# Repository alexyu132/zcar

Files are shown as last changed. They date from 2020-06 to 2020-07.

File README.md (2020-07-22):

This is a 1/28 scale RC chassis designed to be compatible with Kyosho MINI-Z body shells. Current version fits 90mm (M) wheelbase shells.

Video: https://www.youtube.com/watch?v=_t0HLC2bZMU

zcar image

## Features: 
- Independent front suspension and hinged rear suspension
- Ackermann steering geometry with 45 degree max steering angle
- Uses common and cheap parts (625 bearings, M3 hardware)
- Low part count and variety - only 3 different screw lengths needed; locknuts everywhere

## New in 1.1:
- More robust rear bearing assembly
- Front suspension travel reduced to prevent scraping
- Redesigned front body mount for increased ground clearance
- Reduced height of motor mount and rear suspension frame to fit lower profile shells

## Non-printed Parts List

|  Part | Quantity | Notes  |
|---|---|---|
|  M3x20mm button head screw | 7  | |
|  M3x14mm button head screw | 2 | |
|  M3x10mm button head screw | 8  | |
|  M3 lock nut | 17 | |
| 625 bearing | 4 | |
| 130 size brushed motor, 2s compatible | 1 | |
| SG90 micro servo | 1 | |
| Compression spring, ~4mm OD, ~5mm length | 2 | For front suspension. Softer springs are better.  Springs from multicolor retractable pens work well here when cut to length. Ordinary pen springs are too stiff. |
| Compression spring, ~4mm OD, ~22mm length | 2 | For rear suspension. Springs from multicolor retractable pens work well here. Can cut to length or leave uncut for different suspension stiffnesses.|
| Venom Fly 300mah 2S battery or RDQ Series 2S 350mAh LiHV battery | 1 | Batteries up to approx. 45x23x16mm should fit |
| Small brushed ESC, 2S compatible | 1 |
| Small radio receiver | 1 | 2 channels or more, smaller than approx 34x22x13mm. Flysky GR3E works if decased. |
| MINI-Z shell | 1 | Tested with Kyosho MZQ101 AE86 shell |
| MINI-Z tires | 4 | 8.5mm width, 25mm OD, 20mm ID. The tires that come with MINI-Z shells work fine. |

## Printing Notes:
###  Settings
#### Resolution: 0.1-0.15mm

#### Infill: 25% or higher

#### Vertical perimeters: 3 or more

#### Horizontal perimeters: 4 or more

#### Supports: Off
Most of the printed parts are split into 2 prearranged trays. **Print tray1.stl at 0.15mm layer height and tray2.stl at 0.1mm layer height**. Make sure your printer has good layer adhesion, as some parts have a small bed contact area and can warp or detach easily.

The front wheels have a cylindrical piece of built-in support on the inside of the wheel. To remove, use pliers to grip the support and pull straight out without twisting.

The motor mount and gears are located in the geartrains subfolder in the STL folder. **There are currently 4 gear ratios available: 13T:42T, 11T:43T, 10T:43T, and 9T:43T**. Generally a lower gear ratio (fewer teeth on motor pinion) is preferred unless your motor is designed for low speed/high torque.

For each gearing option, there are loose and tight motor mounts available due to 130 motors varying slightly in size. The loose mount fits motors that are 15.4mm wide across the flats, while the tight mount fits 15mm wide motors. If you decide to change the gearing, make sure to also print a matching motor mount, as motor mounts are not interchangeable among different geartrains. For more powerful motors, you may need to print the pinion and motor mount in ABS or PETG to prevent heat-induced softening.

## Assembly
Coming soon

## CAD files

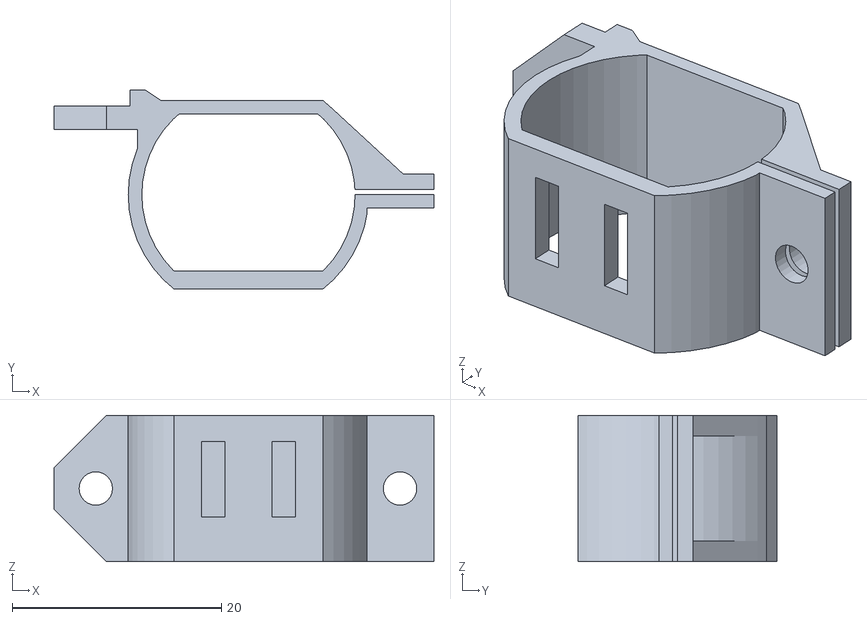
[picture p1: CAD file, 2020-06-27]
stl/geartrains/10T-43T/motor_mount_10_43_tight.stl
36.4 x 19.0 x 14.0

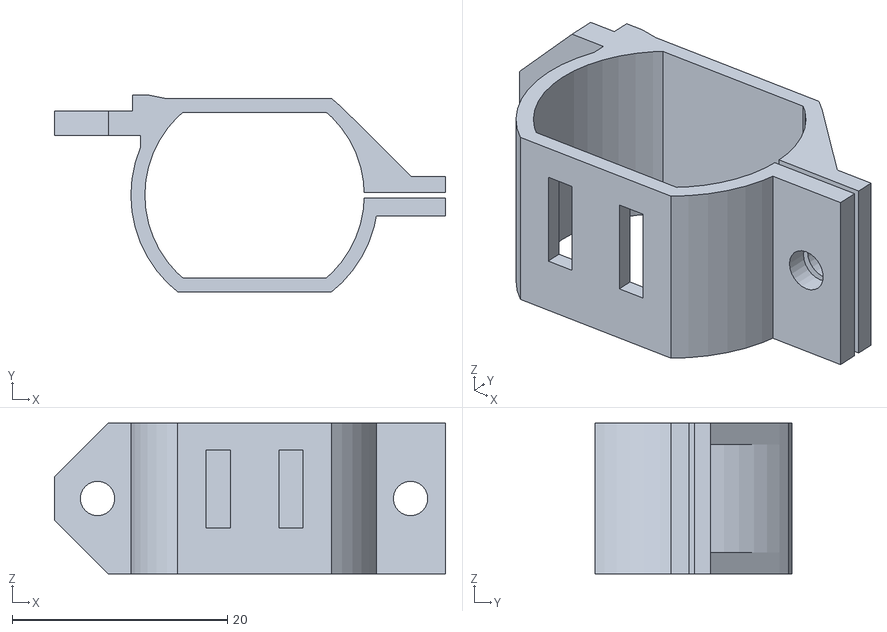
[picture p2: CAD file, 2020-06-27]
stl/geartrains/13T-42T/motor_mount_13_42_loose.stl
36.4 x 18.3 x 14.0

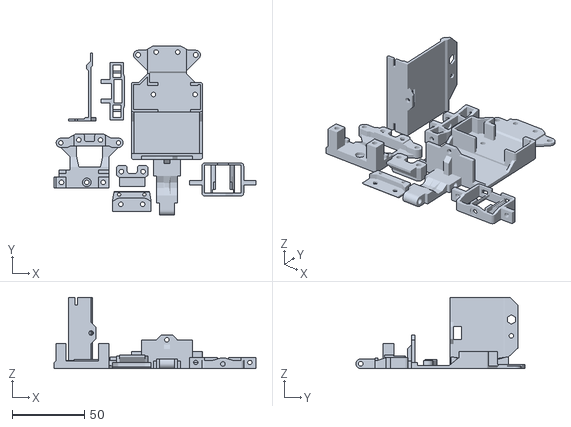
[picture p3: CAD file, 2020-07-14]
stl/tray1.stl
140.2 x 117.4 x 49.5

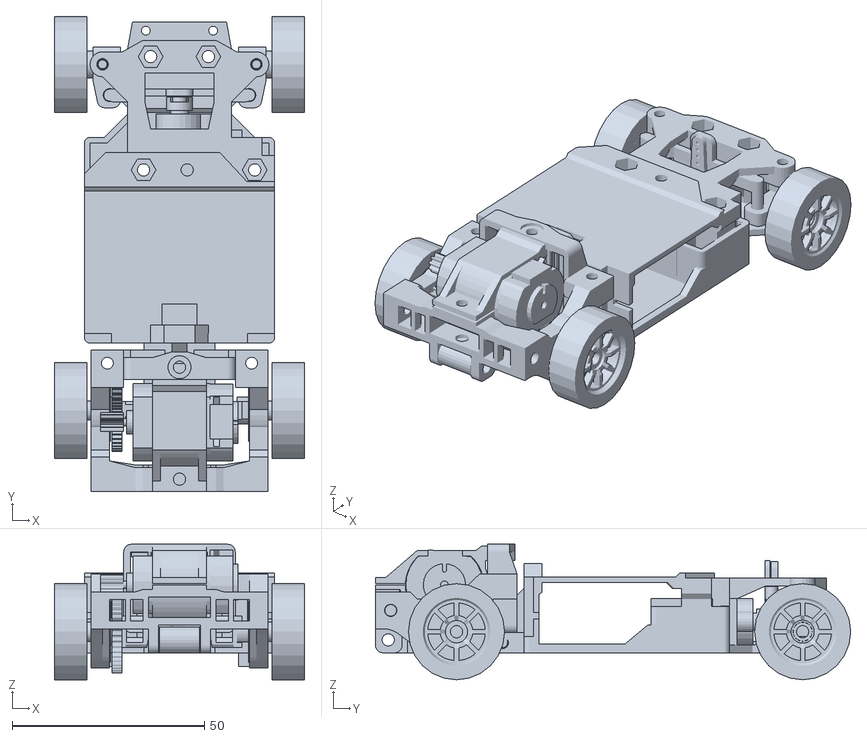
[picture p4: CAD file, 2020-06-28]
stl/zcar.stl
65.0 x 123.6 x 35.2

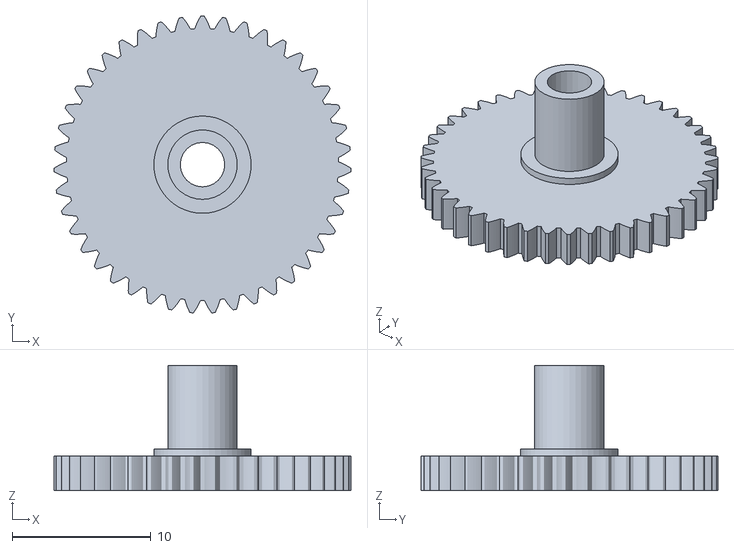
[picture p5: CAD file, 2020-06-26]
stl/geartrains/10T-43T/43T_gear.stl
21.4 x 21.4 x 9.00

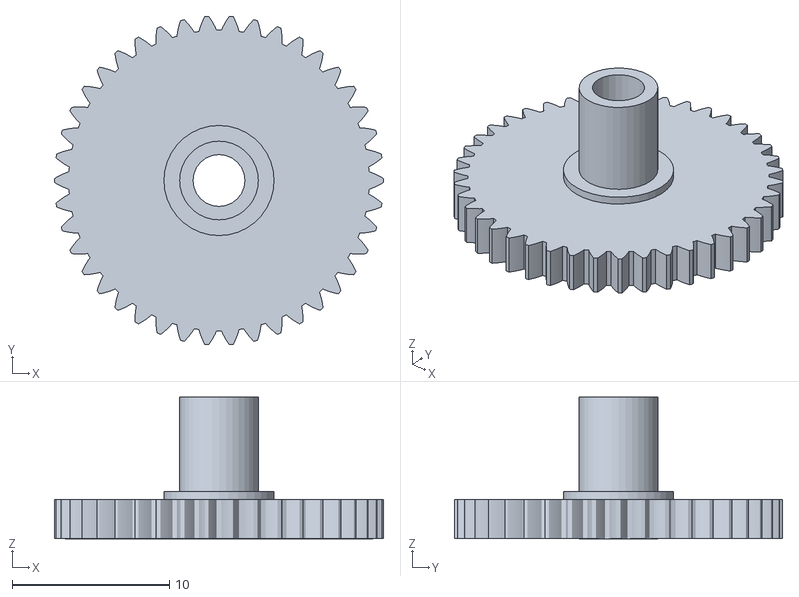
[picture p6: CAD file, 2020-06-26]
stl/geartrains/13T-42T/42T_gear.stl
20.9 x 20.9 x 9.01

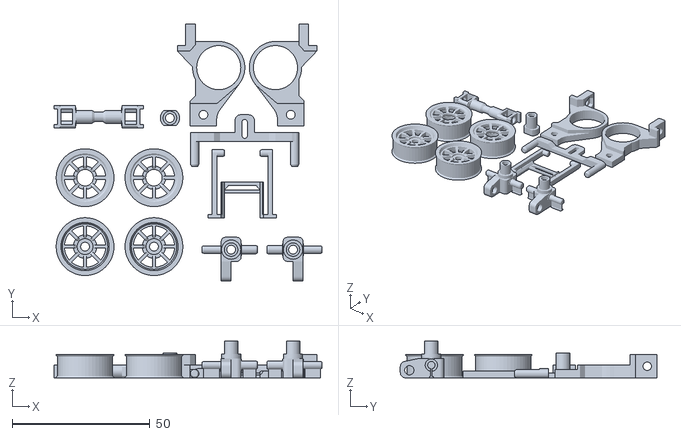
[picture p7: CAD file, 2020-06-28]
stl/tray2.stl
97.2 x 93.1 x 13.4

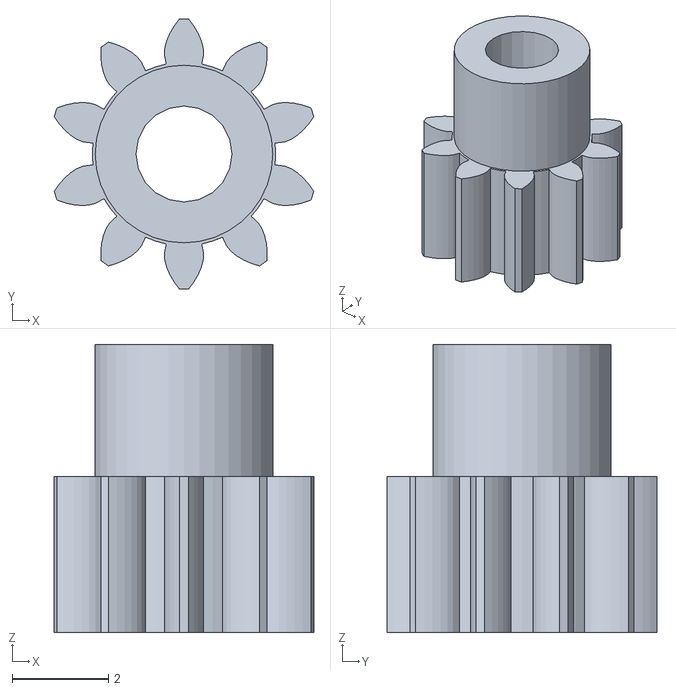
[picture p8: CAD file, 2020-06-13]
stl/geartrains/10T-43T/10T_pinion.stl
5.41 x 5.63 x 6.00

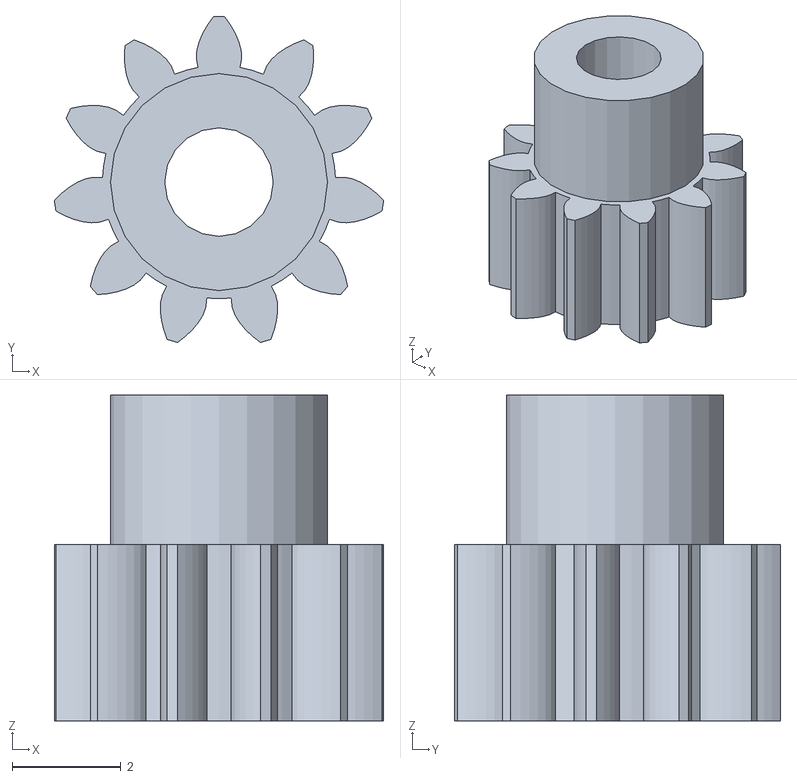
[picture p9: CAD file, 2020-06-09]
stl/geartrains/11T-43T/11T_pinion.stl
6.07 x 6.01 x 6.00

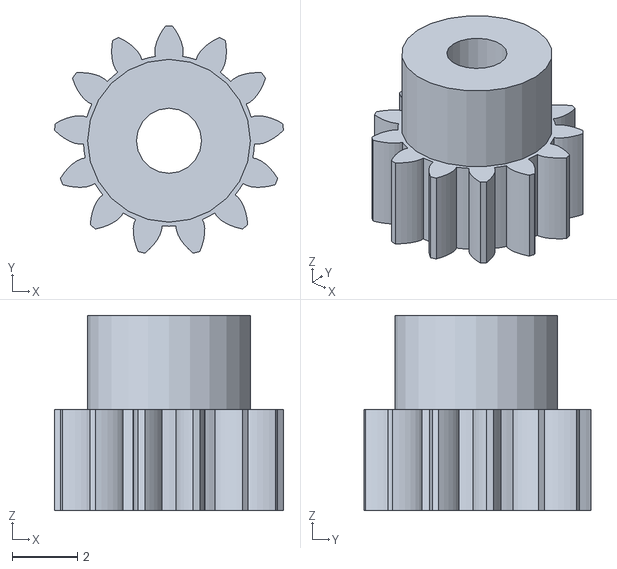
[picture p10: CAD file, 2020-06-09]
stl/geartrains/13T-42T/13T_pinion.stl
7.03 x 6.98 x 6.00

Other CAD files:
stl/geartrains/11T-43T/motor_mount_11_43_tight.stl
stl/geartrains/9T-43T/motor_mount_9_43_loose.stl
stl/geartrains/10T-43T/motor_mount_10_43_loose.stl
stl/geartrains/11T-43T/motor_mount_11_43_loose.stl
stl/geartrains/13T-42T/motor_mount_13_42_tight.stl
stl/geartrains/9T-43T/motor_mount_9_43_tight.stl
stl/geartrains/11T-43T/43T_gear.stl
stl/geartrains/9T-43T/9T_pinion.stl
stl/tpu_tire.stl
zcar.skp

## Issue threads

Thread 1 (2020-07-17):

Rear Bearing Hubs

bryanmonahan, 2020-07-17:
hey Alex,  this is an amazing design.  My friend and I have printed a few and are messing around with them

1. found that the rear bearing holders do not maintain hold on the bearings when heated.   am looking at possibly adding a lip around them to maintain control of the bearing, but then must add a washer on the inside to space out the gear from hitting it.

unknown yet.

alexyu132, 2020-07-17:
What's causing the rear bearings to heat up?

If you switch to the 1.1 branch, I've redesigned the rear bearings to be press fit, which should be less flimsy than the previous design (no lip, but I can add one if there are still loosening issues). You could try switching to that, or look into using a higher temp material like PETG or ABS.

bryanmonahan, 2020-07-17:
I am using a complete petg build at the moment...

I have no idea whats happening, but myself and another beta tester are having the same issues on two different builds.

1.1 branch...?  sorry, github is new language for me.  ill go dig around.

alexyu132, 2020-07-17:
If you go to the main page there should be a small dropdown menu on the left that says 'master'. Click that and you can switch to the 1.1 branch.

bryanmonahan, 2020-07-17:
OK, found.

unknown if this will help.

What is happening, during racing when cornering, the bearings are slipping out under full speed.  the car then exits the turn and alignment is off.   Ive taken to epoxy to keep them in place.

Ive slammed a small ridge on the inside to help keep the bearing from shifting, and was about to print it till you told me about v1.1

I think your new design may eliminate it, but unknown what exactly is causing the issue.   Ill print the new version and the rear assembly block it appears to connect to instead of the old method and give that a try.

Thanks for your work with this.

We have also modified the wheels to a simpler design (no spokes) and extended the rear to 11mm.

Looking at modifying the battery cover to create a lower mounting point for the receiver and ESC to lower center of gravity.

This is by far, the simplest and most effective 3d print 1/28th scale car ive found and printed in about 2 years of doing so.   great work.

alexyu132, 2020-07-17:
Thanks!

Which battery are you using? The one I have pretty much fills the entire battery area so lowering the CG would be difficult without dropping the overall ride height.

bryanmonahan, 2020-07-17:
a 3.7... but my theory is if i flip it on its side, i can cram the battery esc and rx into the same space,   but thats later.

I am reprinting parts in taulman tech-g now, i like the new rear end idea from 1.1, i think the that connecting the rear hubs to two different axis will result in a lot more stability.

if you would like to talk, im on discord - scapegoatRB#8166, my friend and I would be happy to help you at least destroy parts to see if they work.

alexyu132, 2020-07-17:
I'd prefer communicating via GitHub issues since it'll make it easier to track problems and suggested improvements. If the new press-fit design fixes the problem, we can close out this issue, but otherwise I can look into adding a lip to the bearing block.

Closed 2020-07-23.

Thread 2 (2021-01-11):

CAD file and assembly instructions

unauwen, 2021-01-11:
Hey, I really like this project and already started printing the components. But I dont know exactly how to assemble the car. Could you add a few pictures of every side? I would like to cusomize it, would it be possible to get the CAD files?
With kind regards
Unauwen

alexyu132, 2021-01-13:
There are some pictures on the Thingiverse page, as well as an STL of the complete assembly. I designed this in SketchUp, so the CAD file is the SKP file in this repo.

unauwen, 2021-01-13:
Thanks for your reply, maybe some photos of the back Suspension and/or the front steering would be helpfull for other makers, but I figured it out with trial and error. Thanks for the design

Closed 2021-01-13.

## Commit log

2020-05-23 initial work
    [zcar.skp]
2020-05-25 rear axle work
    [zcar.skp]
2020-05-25 suspension adjustments, rear axle work
    [zcar.skp]
2020-05-25 rear suspension work
    [zcar.skp]
2020-05-25 rear suspension
    [zcar.skp]
2020-05-25 fix gear clearance
    [zcar.skp]
2020-05-25 top plate
    [zcar.skp]
2020-05-25 tweak bottom plate
    [zcar.skp]
2020-05-25 reduce material usage
    [zcar.skp]
2020-05-25 small tweaks
    [zcar.skp]
2020-05-25 add supports to steering knuckles
    [zcar.skp]
2020-05-25 rear body tweaks
    [zcar.skp]
2020-05-25 tweak rear
    [zcar.skp]
2020-05-26 Add tire retaining ring on wheels
    [zcar.skp]
2020-05-26 Modify wheel retaining ring, minor body tweak
    [zcar.skp]
2020-05-26 Add readme, minor body tweaks
    [zcar.skp]
2020-05-27 make chassis more compact, fix motor mounting position
    [zcar.skp]
2020-05-27 reduce frame width
    [zcar.skp]
2020-05-27 switch to smaller battery to save space
    [zcar.skp]
2020-05-27 add tire
    [zcar.skp]
2020-05-28 increase track width by 1mm
    [zcar.skp]
2020-05-28 lower gear ratio to 13T/42T
    [zcar.skp]
2020-05-29 minor lower frame tweak
    [zcar.skp]
2020-05-29 Improve wheel support layer adhesion, fix rear wheel shaft interface
    [zcar.skp]
2020-05-29 increase sill height
    [zcar.skp]
2020-05-31 lengthen steering rack pins
    [zcar.skp]
2020-05-31 test better wheel supports
    [zcar.skp]
2020-06-01 small printability and clearance adjustments
    [zcar.skp]
2020-06-01 fix dimension errors, improve supports
    [zcar.skp]
2020-06-01 adjust steering rack tolerance
    [zcar.skp]
2020-06-01 lengthen rear suspension slider
    [zcar.skp]
2020-06-01 additional rear spring length
    [zcar.skp]
2020-06-01 shell mounts
    [zcar.skp]
2020-06-02 fix servo mount
    [zcar.skp]
2020-06-02 reduce rear suspension travel
    [zcar.skp]
2020-06-02 add rear suspension alignment tabs
    [zcar.skp]
2020-06-02 fix battery dimensions
    [zcar.skp]
2020-06-02 improve shell fit
    [zcar.skp]
2020-06-03 wheel option for non printed tires
    [zcar.skp]
2020-06-03 reduce track width by 2mm
    [zcar.skp]
2020-06-03 reduce rear suspension spring length, lower top plate
    [zcar.skp]
2020-06-03 0.5mm more front suspension travel
    [zcar.skp]
2020-06-03 slightly thicken sills
    [zcar.skp]
2020-06-04 fix gear clearance error
    [zcar.skp]
2020-06-04 rear assembly improvements
    [zcar.skp]
2020-06-04 tweak steering rack clearances
    [zcar.skp]
2020-06-05 slightly recess rear wheel bolt
    [zcar.skp]
2020-06-06 Add stls, update readme
    [tray1.stl, tray2.stl, zcar.stl]
2020-06-07 slightly extend rear suspension slider
    [tray1.stl, zcar.skp]
2020-06-09 Allow thinner springs to be used; add tighter motor mount
    [motor_mount_tight.stl, tray1.stl, tray2.stl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]
2020-06-09 Add 11T/43T gear ratio option, update readme, minor clearance adjustments
    [11T_pinion.stl, 13T_pinion.stl, 42T_gear.stl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]
2020-06-09 add tpu tire stl
    [tpu_tire.stl, zcar.skp]
2020-06-10 Tweak 11T/43T gear clearance
    [motor_mount_loose.stl, motor_mount_tight.stl, zcar.skp]
2020-06-10 Update stl
    [zcar.skp, zcar.stl]
2020-06-13 Add 10T/43T ratio, make motor mount names more descriptive
    [10T_pinion.stl, 43T_gear.stl, motor_mount_10_43_loose.stl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]
2020-06-14 strengthen rear bearing clamps, tweak steering rack clearances
    [tray2.stl]
2020-06-17 Add 9T:43T ratio, adjust loose motor mount clearance
    [43T_gear.stl, 9T_pinion.stl, motor_mount_10_43_loose.stl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]
2020-06-17 Fix small error in motor mounts
    [motor_mount_10_43_loose.stl, motor_mount_10_43_tight.stl, motor_mount_9_43_loose.stl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]
2020-06-19 reduce tooth clearance on 9T/43T
    [motor_mount_9_43_loose.stl, motor_mount_9_43_tight.stl]
2020-06-21 Add cooling vents to motor mounts
    [motor_mount_10_43_loose.stl, motor_mount_10_43_tight.stl, motor_mount_13_42_loose.stl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]
2020-06-26 tighten rear bearing clearances
    [42T_gear.stl, 43T_gear.stl, tray2.stl]
2020-06-26 Decrease front suspension travel by 0.75mm
    [tray1.stl, tray2.stl]
2020-06-27 make right rear axle end more compact
    [tray2.stl]
2020-06-27 tighten screw clearances on rear axle parts
    [tray1.stl, tray2.stl]
2020-06-27 lower overall height of rear suspension assembly
    [motor_mount_10_43_loose.stl, motor_mount_10_43_tight.stl, motor_mount_11_43_loose.stl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]
2020-06-27 tweak rear axle shaft
    [tray2.stl]
2020-06-28 redesign front mount for more ground clearance
    [tray1.stl]
2020-06-28 rework rear bearing blocks and hinge
    [tray1.stl, tray2.stl, zcar.skp]
2020-06-29 slightly adjust 9T/43T gear mesh
    [motor_mount_9_43_loose.stl, motor_mount_9_43_tight.stl, zcar.skp]
2020-07-14 FIx tray1
    [tray1.stl]
